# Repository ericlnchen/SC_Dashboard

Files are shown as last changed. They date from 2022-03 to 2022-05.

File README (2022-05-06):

SC Racing Dashboard

Made with love for best elec lead, Seth Krieger

Designed by Eric Chen
Thanks, to Jack Eagan and Stephen Baker for technical support understanding the teensy and screen

Special Thanks for Vihan Raj for developing CAN together and hardware debugging the hell outta the car and Manas Shah for optimization and organization

Current stage:
	- All critical functions are completed for Driver's Dashboard 
	- Implementing customized CAN code from the ECU to Dash
	- Inheritance is now available for any derived class on display class
	- Debug is half done
	- CAN works with old ECU AEM Infinity 7
	- Includes a namespace for SCRCAN

Future stages:
	- Touchscreen capability
	- Other sensor data such as tyre temps and throttle position
	- Other modes for the car
	- Developing a SC_CAN library for use in other programs

Inheritance Chart:

display.h is a base class sending info to the dash
	-> debug_screen.h is a public derived class from display.h

main.cpp has a display and SRCCAN

This directory is intended for PlatformIO Unit Testing and project tests.

Unit Testing is a software testing method by which individual units of
source code, sets of one or more MCU program modules together with associated
control data, usage procedures, and operating procedures, are tested to
determine whether they are fit for use. Unit testing finds problems early
in the development cycle.

More information about PlatformIO Unit Testing:
- https://docs.platformio.org/page/plus/unit-testing.html

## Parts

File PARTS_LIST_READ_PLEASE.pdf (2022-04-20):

Display:
- Touch Graphics LCD Display 240x128 Module T6963 Compatible RA6963
- https://www.buydisplay.com/download/manual/ERM240128-2_Series_Datasheet.pdf
- https://www.buydisplay.com/download/ic/RA6963.pdf
Processor:
- Teensy 3.5

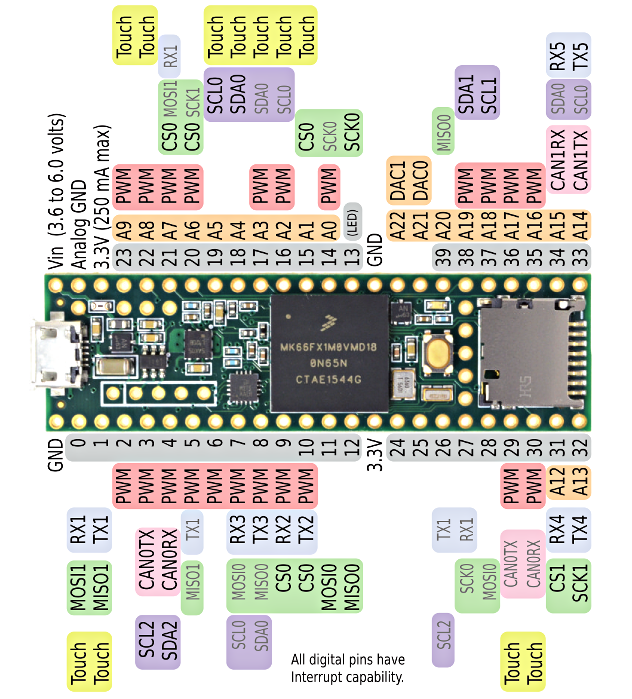
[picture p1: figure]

Transceiver:
- MCP2562FD
- High-speed CAN FD Transceiver with Standby Mode and VIO Pin

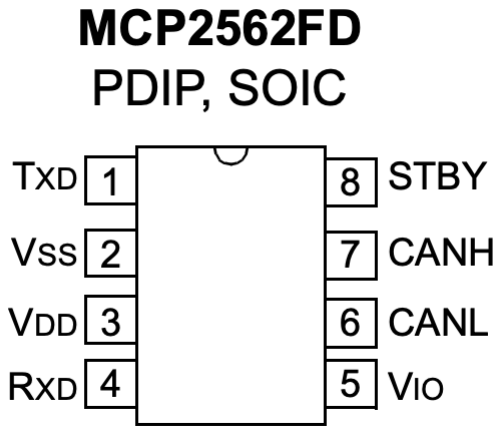
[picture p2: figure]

Voltage Regulators - Linear:
- L7805CV by STMicroelectronics
- Part Number: 497-1443-5-ND

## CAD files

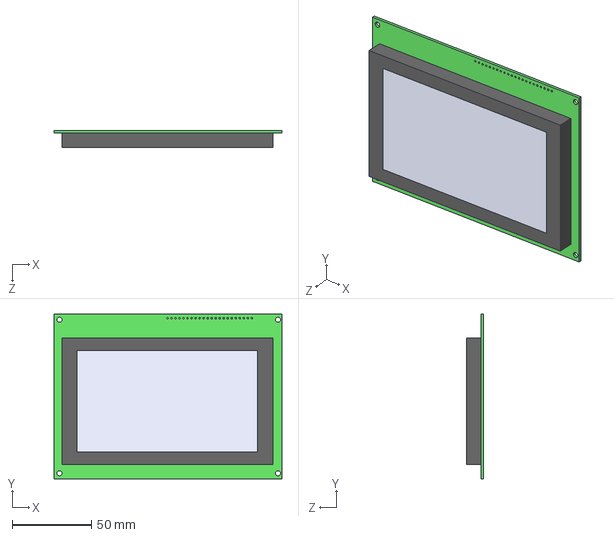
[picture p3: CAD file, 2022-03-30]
Imported Performance Logger.PrjPcb/BiggDisplay.STEP
144.0 x 104.0 x 11.0 mm

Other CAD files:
Imported Performance Logger.PrjPcb/BiggDisplay.SLDPRT

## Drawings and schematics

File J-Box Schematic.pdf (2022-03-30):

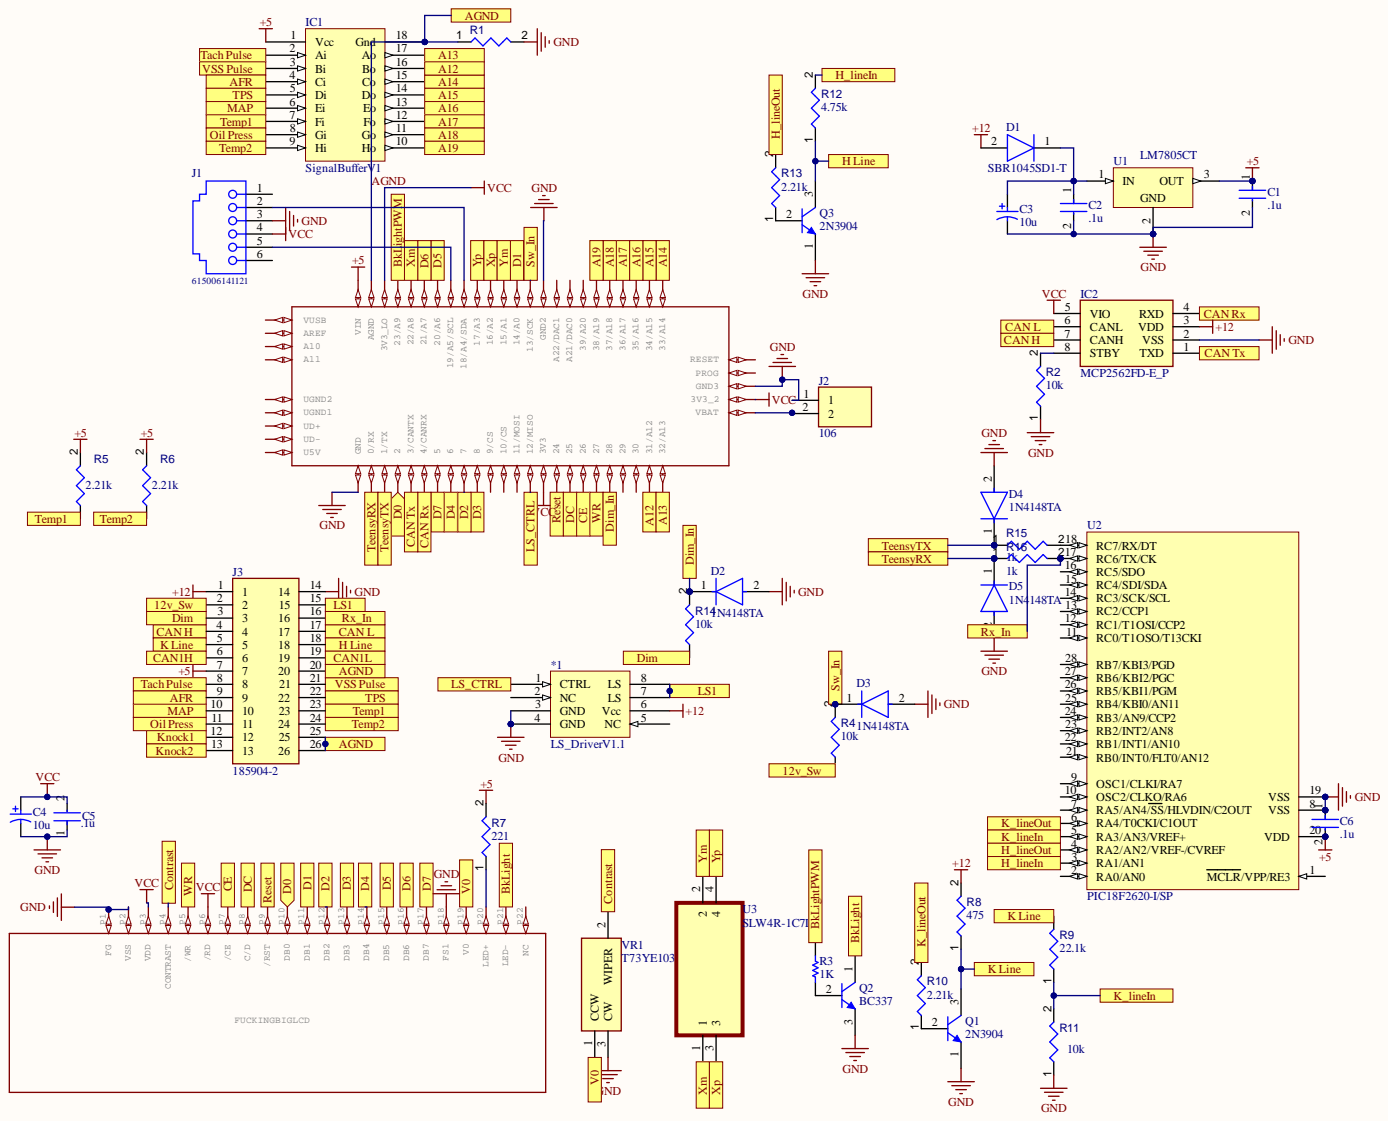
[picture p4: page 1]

6 | +5

RC0/T1OSO/T13CKI 11 RC1/T1OSI/CCP2 12 RC2/CCP1 13 RC3/SCK/SCL 14 RC4/SDI/SDA 15 RC5/SDO 16 RC6/TX/CK 17 RC7/RX/DT 18

Dim | Rx_In

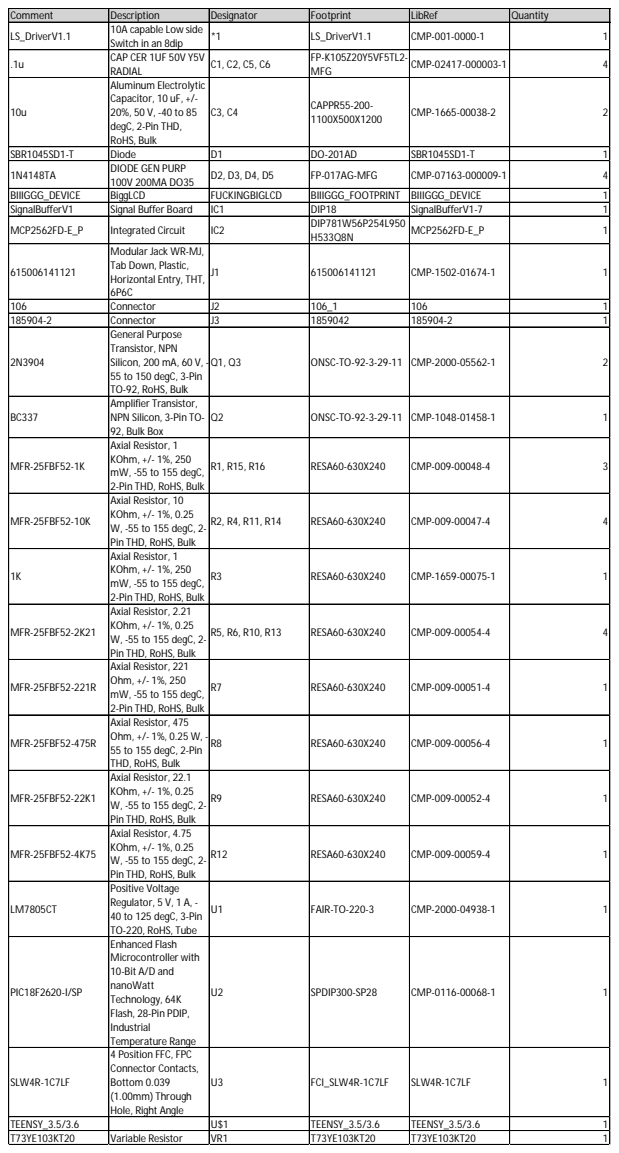
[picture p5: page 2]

Comment | Description | Designator | Footprint | LibRef | Quantity
LS_DriverV1.1 | 10A capable Low side Switch in an 8dip | *1 | LS_DriverV1.1 | CMP-001-0000-1 | 1

.1u | CAP CER 1UF 50V Y5V RADIAL | C1, C2, C5, C6 | FP-K105Z20Y5VF5TL2-MFG | CMP-02417-000003-1 | 4

10u | Aluminum Electrolytic Capacitor, 10 uF, +/-20%, 50 V, -40 to 85 degC, 2-Pin THD, RoHS, Bulk | C3, C4 | CAPPR55-200-1100X500X1200 | CMP-1665-00038-2 | 2

SBR1045SD1-T | Diode | D1 | DO-201AD | SBR1045SD1-T | 1
1N4148TA | DIODE GEN PURP 100V 200MA DO35 | D2, D3, D4, D5 | FP-017AG-MFG | CMP-07163-000009-1 | 4

BIIIGGG_DEVICE | BiggLCD | FUCKINGBIGLCD | BIIIGGG_FOOTPRINT | BIIIGGG_DEVICE | 1
SignalBufferV1 | Signal Buffer Board | IC1 | DIP18 | SignalBufferV1-7 | 1
MCP2562FD-E_P | Integrated Circuit | IC2 | DIP781W56P254L950 H533Q8N | MCP2562FD-E_P | 1

615006141121 | Modular Jack WR-MJ, Tab Down, Plastic, Horizontal Entry, THT, 6P6C | J1 | 615006141121 | CMP-1502-01674-1 | 1

106 | Connector | J2 | 106_1 | 106 | 1
185904-2 | Connector | J3 | 1859042 | 185904-2 | 1
2N3904 | General Purpose Transistor, NPN Silicon, 200 mA, 60 V, -55 to 150 degC, 3-Pin TO-92, RoHS, Bulk | Q1, Q3 | ONSC-TO-92-3-29-11 | CMP-2000-05562-1 | 2

BC337 | Amplifier Transistor, NPN Silicon, 3-Pin TO-92, Bulk Box | Q2 | ONSC-TO-92-3-29-11 | CMP-1048-01458-1 | 1

MFR-25FBF52-1K | Axial Resistor, 1 KOhm, +/- 1%, 250 mW, -55 to 155 degC, 2-Pin THD, RoHS, Bulk | R1, R15, R16 | RESA60-630X240 | CMP-009-00048-4 | 3

MFR-25FBF52-10K | Axial Resistor, 10 KOhm, +/- 1%, 0.25 W, -55 to 155 degC, 2-Pin THD, RoHS, Bulk | R2, R4, R11, R14 | RESA60-630X240 | CMP-009-00047-4 | 4

1K | Axial Resistor, 1 KOhm, +/- 1%, 250 mW, -55 to 155 degC, 2-Pin THD, RoHS, Bulk | R3 | RESA60-630X240 | CMP-1659-00075-1 | 1

MFR-25FBF52-2K21 | Axial Resistor, 2.21 KOhm, +/- 1%, 0.25 W, -55 to 155 degC, 2-Pin THD, RoHS, Bulk | R5, R6, R10, R13 | RESA60-630X240 | CMP-009-00054-4 | 4

MFR-25FBF52-221R | Axial Resistor, 221 Ohm, +/- 1%, 250 mW, -55 to 155 degC, 2-Pin THD, RoHS, Bulk | R7 | RESA60-630X240 | CMP-009-00051-4 | 1

MFR-25FBF52-475R | Axial Resistor, 475 Ohm, +/- 1%, 0.25 W, -55 to 155 degC, 2-Pin THD, RoHS, Bulk | R8 | RESA60-630X240 | CMP-009-00056-4 | 1

MFR-25FBF52-22K1 | Axial Resistor, 22.1 KOhm, +/- 1%, 0.25 W, -55 to 155 degC, 2-Pin THD, RoHS, Bulk | R9 | RESA60-630X240 | CMP-009-00052-4 | 1

MFR-25FBF52-4K75 | Axial Resistor, 4.75 KOhm, +/- 1%, 0.25 W, -55 to 155 degC, 2-Pin THD, RoHS, Bulk | R12 | RESA60-630X240 | CMP-009-00059-4 | 1

LM7805CT | Positive Voltage Regulator, 5 V, 1 A, -40 to 125 degC, 3-Pin TO-220, RoHS, Tube | U1 | FAIR-TO-220-3 | CMP-2000-04938-1 | 1

PIC18F2620-I/SP | Enhanced Flash Microcontroller with 10-Bit A/D and nanoWatt Technology, 64K Flash, 28-Pin PDIP, Industrial Temperature Range | U2 | SPDIP300-SP28 | CMP-0116-00068-1 | 1

SLW4R-1C7LF | 4 Position FFC, FPC Connector Contacts, Bottom 0.039 (1.00mm) Through Hole, Right Angle | U3 | FCI_SLW4R-1C7LF | SLW4R-1C7LF | 1

TEENSY_3.5/3.6 | | U$1 | TEENSY_3.5/3.6 | TEENSY_3.5/3.6 | 1
T73YE103KT20 | Variable Resistor | VR1 | T73YE103KT20 | T73YE103KT20 | 1

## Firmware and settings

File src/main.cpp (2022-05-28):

#include <display.h>
// #include <SCRLOGGER.hpp>
#include <SCRCAN.hpp>
#include <ADC.h>
#include <ADC_util.h>
#include <SPI.h>
#include <globalData.h>
#include <avr/io.h>
#include <avr/interrupt.h>

//  Test Variables
int cutoff = 6000;
int lapTime[3] = {0,0,0};
char gears[6] = {'N','1','2','3','4','5'};

// IMPORTANT objects
Display driver;

// scheduling variables
unsigned long lastRpmUpdate = 0;
unsigned long lastCTempUpdate = 0;
unsigned long lastOTempUpdate = 0;
unsigned long lastOpressureUpdate = 0;
unsigned long lastVoltUpdate = 0;
unsigned long lastLogUpdate = 0;

IntervalTimer CANRead;
// IntervalTimer LOGWrite;
void setup() {
  Serial.println("1");
  // initializeSysClock();
  // initializeSD();
  Serial.begin(9600);
  SPI.setMOSI(11); 
  SPI.setMISO(12); 
  SPI.setSCK(13);
  pinMode(13, OUTPUT);
  digitalWrite(13, HIGH);
  driver = Display(); // Driver Display
  driver.initializeDisplay();
  CANRead.begin(SCRCAN::getMessage, 32);
  // LOGWrite.begin(logData, 32);
  driver.sendAll();
}

void loop() {

  //  assigning CAN values to stored variables makes sure read and display values are equal
  current_throttle = SCRCAN::throttle;
  current_coolantTemp = SCRCAN::coolant_temp;
  current_oilTemp = SCRCAN::oil_temp;
  current_oilPressure = SCRCAN::oil_pressure;
  current_battery = SCRCAN::voltage;

  // if(millis() - lastLogUpdate > 500){
  //   logData();
  //   lastLogUpdate = millis();
  // }

  Serial.println(current_battery);

  // only updates if theres a difference, so bus wont get cluttered
  if(current_throttle != last_throttle){
    driver.drawMph(current_throttle);
    last_throttle = current_throttle;
    driver.sendAll();
  }

  // // UPDATES COOLANT TEMPERATURE
  // if(millis() - lastCTempUpdate > 1000 && current_coolantTemp != last_coolantTemp){
    
  //   if(current_coolantTemp < 100) driver.display_coolantTemp(current_coolantTemp, true);
  //   else driver.display_coolantTemp(current_coolantTemp, false);
    
  //   last_coolantTemp = current_coolantTemp;
  //   lastCTempUpdate = millis();
  //   driver.u8g2.updateDisplay();
  // }

  // // UPDATES OIL TEMPERATURE 
  // if(millis() - lastOTempUpdate > 1500 && current_oilTemp != last_oilTemp){
    
  //   if(current_oilTemp < 100) driver.display_oilTemp(current_oilTemp, true);
  //   else driver.display_oilTemp(current_oilTemp, false);
    
  //   last_oilTemp = current_oilTemp;
  //   lastOTempUpdate = millis();
  //   driver.u8g2.updateDisplay();
  // }

  // // UPDATES OIL PRESSURE
  // if(millis() - lastOpressureUpdate > 1500 && current_oilPressure != last_oilPressure){
    
  //   if(current_oilPressure < 90 && current_oilPressure >= 30) driver.display_oilPressure(current_oilPressure, true);
  //   else driver.display_oilPressure(current_oilPressure, false);
    
  //   last_oilPressure= current_oilPressure;
  //   lastOpressureUpdate = millis();
  //   driver.u8g2.updateDisplay();
  // }

  // // UPDATES BATTERY VOLTAGE
  // if(millis() - lastVoltUpdate > 2000 && current_battery != last_battery){
    
  //   if(current_battery > 10.5) driver.display_batteryVoltage(current_battery, true);
  //   else driver.display_batteryVoltage(current_battery, false);
    
  //   last_battery= current_battery;
  //   lastVoltUpdate = millis();
  //   driver.u8g2.updateDisplay();
  // }
}

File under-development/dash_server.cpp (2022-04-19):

#include <SPI.h>
#include <EthernetV2_0.h>

// Enter a MAC address and IP address for your controller below.
// The IP address will be dependent on your local network:
byte mac[] = { 
  0xDE, 0xAD, 0xBE, 0xEF, 0xFE, 0xED };
IPAddress ip(192,168,1, 177);

// Initialize the Ethernet server library
// with the IP address and port you want to use 
// (port 80 is default for HTTP):
EthernetServer server(80);
#define W5200_CS  10
#define SDCARD_CS 4

void setup() {
 // Open serial communications and wait for port to open:
 Serial.begin(9600);
 pinMode(SDCARD_CS,OUTPUT);
 digitalWrite(SDCARD_CS,HIGH);//Deselect the SD card
  // start the Ethernet connection and the server:
  Ethernet.begin(mac, ip);
  server.begin();
  Serial.print("server is at ");
  Serial.println(Ethernet.localIP());
}


void loop() {
  // listen for incoming clients
  EthernetClient client = server.available();
  if (client) {
    Serial.println("new client");
    // an http request ends with a blank line
    boolean currentLineIsBlank = true;
    while (client.connected()) {
      if (client.available()) {
        char c = client.read();
        Serial.write(c);
        // if you've gotten to the end of the line (received a newline
        // character) and the line is blank, the http request has ended,
        // so you can send a reply
        if (c == '\n' && currentLineIsBlank) {
          // send a standard http response header
          client.println("HTTP/1.1 200 OK");
          client.println("Content-Type: text/html");
          client.println("Connnection: close");
          client.println();
          client.println("<!DOCTYPE HTML>");
          client.println("<html>");
                    // add a meta refresh tag, so the browser pulls again every 5 seconds:
          client.println("<meta http-equiv=\"refresh\" content=\"5\">");
          // output the value of each analog input pin
          for (int analogChannel = 0; analogChannel < 6; analogChannel++) {
            int sensorReading = analogRead(analogChannel);
            client.print("analog input ");
            client.print(analogChannel);
            client.print(" is ");
            client.print(sensorReading);
            client.println("<br />");       
          }
          client.println("</html>");
          break;
        }
        if (c == '\n') {
          // you're starting a new line
          currentLineIsBlank = true;
        } 
        else if (c != '\r') {
          // you've gotten a character on the current line
          currentLineIsBlank = false;
        }
      }
    }
    // give the web browser time to receive the data
    delay(1);
    // close the connection:
    client.stop();
    Serial.println("client disonnected");
  }
}

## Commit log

2022-03-30 first version upload of Eric's dash
    [BiggDisplay.SLDPRT, BiggDisplay.STEP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]
2022-04-03 main current and fuel current added
2022-04-26 refresh only when values change, need to implement millis for instance speed needs to be refreshed more often than coolant
2022-05-20 FLEXCAN and interval timer
2022-05-28 classes touchevent and button work independently. Need to test on a working touchscreen if the two classes work with another.
